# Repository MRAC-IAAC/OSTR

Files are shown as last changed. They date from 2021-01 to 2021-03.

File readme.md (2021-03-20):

SHEDIO [ _Σχέδιο_ ] --
_noun_
- from Greek origin meaning _'plan', 'drawing', 'scheme'_

-------------------------------

## **IAAC - MRAC 01**

## **DRAWING BOT - HARDWARE II SEMINAR**

**- A minibot that draws contours of images on flat surfaces -**

-------------------------------

### **The Drawing Bot**
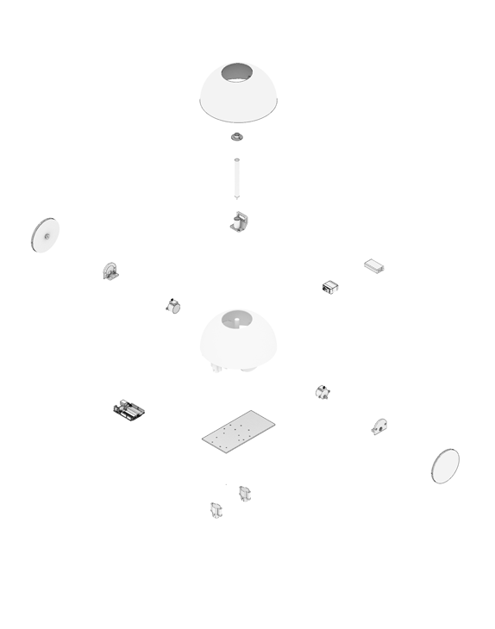
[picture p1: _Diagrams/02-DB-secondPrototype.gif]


-------------------------------

## **GETTING STARTED**

**_Note_**  
For this DIY project, a separate setup of the piCamera (in a box) is in charge of taking the photo that is to be traced by the mini bot.  

Let's do it!

-------------------------------

## **00. HARDWARE**

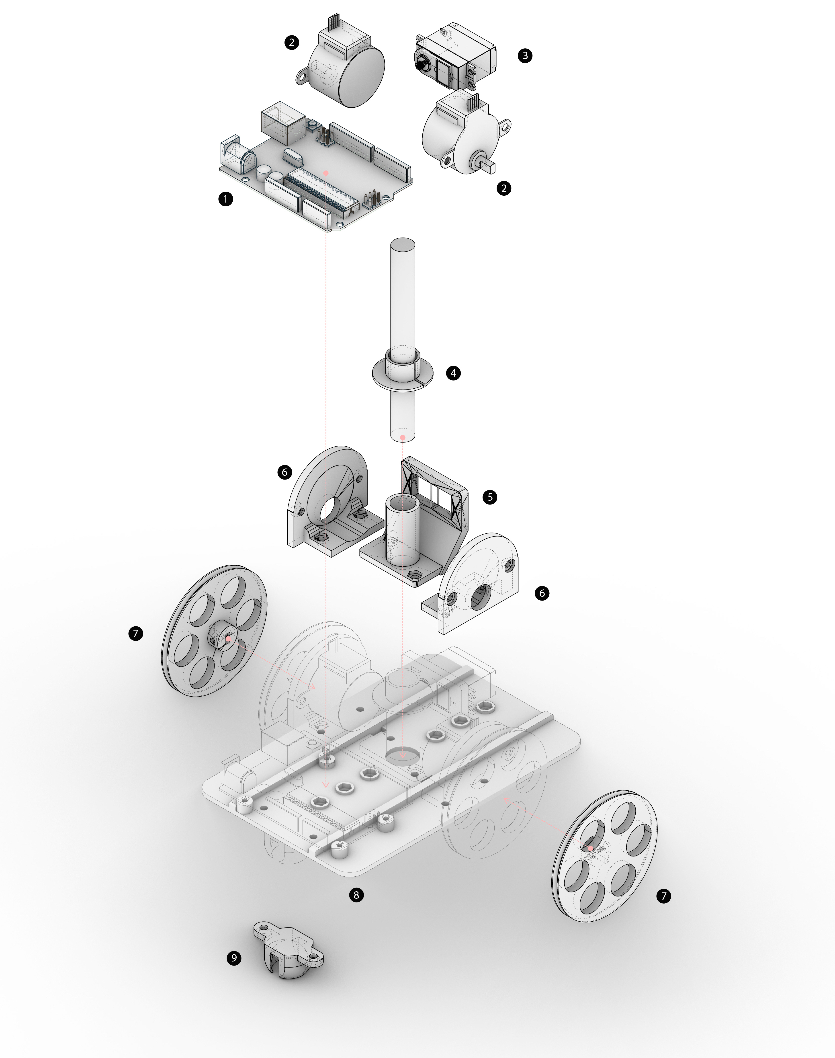
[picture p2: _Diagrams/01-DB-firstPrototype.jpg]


**First Iteration Parts:**  
(1) Arduino Uno  
(2) 28byj-48 Stepper Motor (x2)  
(3) Mini Servo Motor  
(4) Pen Holder  
(5) Servo Motor Holder (controlling the pen’s movement)  
(6) 3D Printed Wheels (x2)  
(7) 3D Printed Board  
(8) Base Plate  
(9) Ball Bearing Holder  

**_Note_**  
An updated model with the latest parts can be found in the _Hardware folder [here](https://github.com/MRAC-IAAC/SHEDIO/tree/master/_Hardware/3D%20Models).

-------------------------------

## **01. ARDUINO**

### **CALIBRATING THE ROBOT & UNDERSTANDING THE SCRIPT**

First things first, we need to translate string commands into wheel movements (controlled by the motors) to be able to establish a clear language with the mini bot. For that, we also need to calibrate it properly.

Follow the tutorial through this [link](https://www.instructables.com/Arduino-Drawing-Robot/).

All necessary arduino codes can be found [here](https://github.com/MRAC-IAAC/SHEDIO/tree/master/_Scripts/Arduino_codes) with comments. 

-------------------------------

## **02. RASPBERRY PI**
**Operating System:** Raspbian GNU/ Linux 10 (buster)

For beginners in Raspberry Pi, [this link](https://www.raspberrypi.org/software/) will be useful to download the imager in order to flash a microSD card with the Raspberry Pi OS. 
The [documentation](https://www.raspberrypi.org/documentation/) tab in the official raspberry pi website is very useful to set up the pi. In the diagrams folder, there is an image of the pinout diagram for the Raspberry Pi 4. 

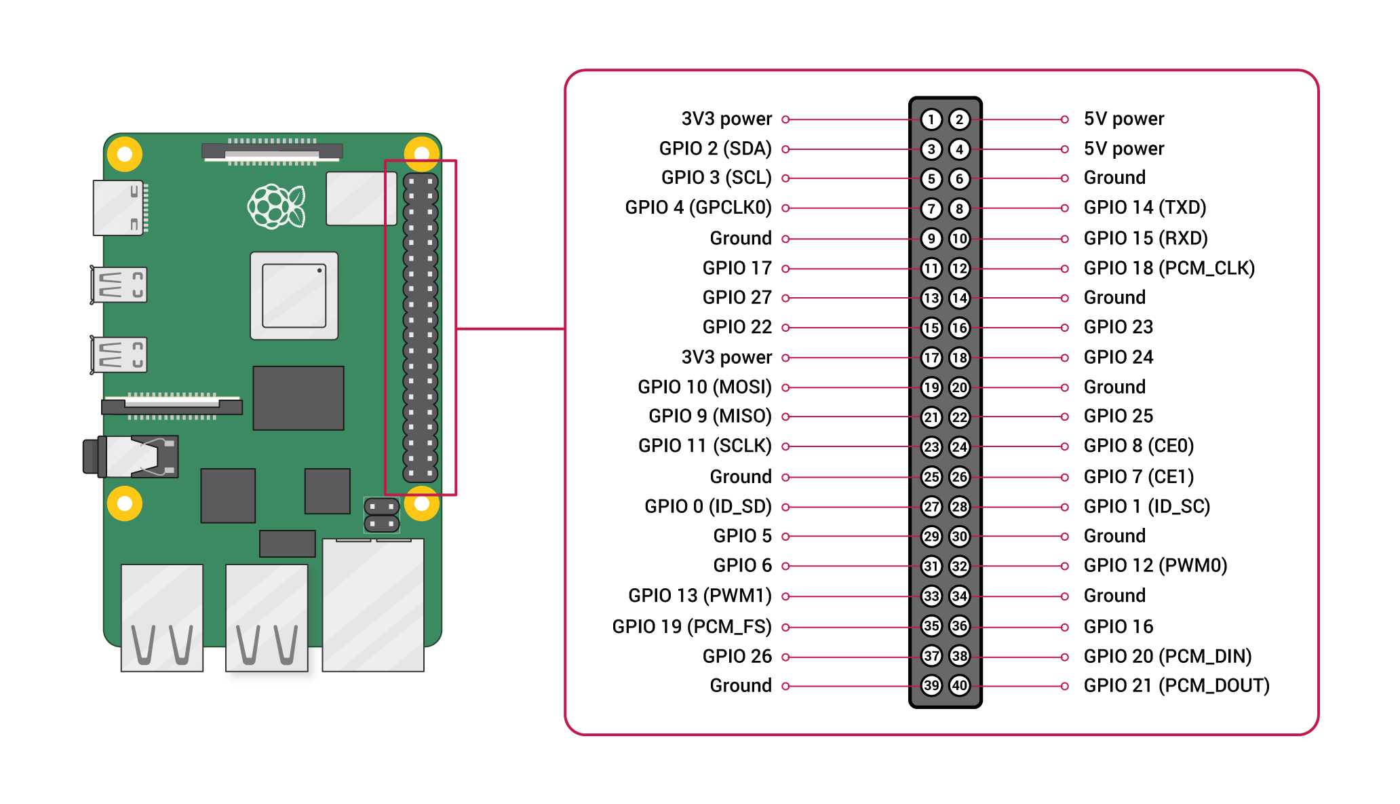
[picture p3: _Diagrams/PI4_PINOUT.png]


The scripts folder should contain a test script to run the pi camera with a touch sensor/ button and another test script for the LED's. 

Some links we used on top of the general set up are as follows:

- PI CAMERA SETUP: https://projects.raspberrypi.org/en/projects/getting-started-with-picamera/2
- BUTTON EXAMPLE: https://raspberrypihq.com/use-a-push-button-with-raspberry-pi-gpio/

### **BLUETOOTH SETUP**
Seting up bluetooth to connect to the HC-06 on the arduino:
This takes a couple of steps to get it to work properly. First, you will have to make sure your Pi is set up with bluetooth properly.

Open a terminal and type
```
bluetoothctl
agent on
default-agent
scan on
```
This will show you a list of available bluetooth networks nearby. You will have to locate the name of your bluetooth and copy the IP address. 

Open a new terminal and do the following:
```
sudo nano /etc/bluetooth/rfcomm.conf
```
add the following and replace the device ip address with yours
```
rfcomm0{
    bind yes;
    device AA:BB:CC:DD:EE:FF
    channel 1;
    comment "connection to bluetooth serial module";
}
```
This will create the necessary file in order for the Raspberry Pi to recognize and connect with the HC-06 Bluetooth Module. You will need to reboot your pi, and once restarted, type the following:

```
bluetoothctl
agent on
default-agent
scan on
```
And in a new terminal:
```
sudo rfcomm connect hci0 AA:BB:CC:DD:EE:FF
```
Now you should be connected to your bluetooth device. In order to connect to your bluetooth module using python, you will have to download the **pyserial** package and your serial port should be defined as (in your python script):
```
 /dev/rfcomm0 
 ```
The name is rfcomm0 because that is the name we wrote in the **rfcomm.conf** file in order for the Raspberry Pi to recognize the bluetooth module. If you need to check, you can type the following into a terminal, which will give you a list of devices connected to your Raspberry Pi via serial port. 
```
lsusb
```

In order to take a picture and translate that into directions, run the **final_script.py** file and then to operate the drawing bot, run the **send_all_the_instructions_to_arduino.py** file (that is where you might have to change the serial port)

**NOTE: The scripts are explained below, and there are notations in each file**

### **OTHER USEFUL LINKS**

Some other links regarding connecting to the Raspberry Pi remotely

To set up a usb connection between the pi and your laptop:
- https://www.hardill.me.uk/wordpress/2019/11/02/pi4-usb-c-gadget/

To set up putty:
- https://www.factoryforward.com/pi-zero-w-headless-setup-windows10-rndis-driver-issue-resolved/

To set up VNC Viewer:
- https://www.raspberrypi.org/documentation/remote-access/vnc/

-------------------------------

## **03. PYTHON**

**_Note_**  
During this project, the following OS and code editors (not necessary) were used:

**Operating Systems:** macOS, Microsoft Windows and Linux  
**Editor 1:** Visual Studio Code, found [here](https://code.visualstudio.com/)  
**Editor 2:** Pycharm, found [here](https://www.jetbrains.com/pycharm/)

For beginners in Python, the [official website](https://www.python.org/about/gettingstarted/) offers getting started tips.  
 **Socratica's** fun youtube [tutorial](https://www.youtube.com/playlist?list=PLi01XoE8jYohWFPpC17Z-wWhPOSuh8Er-) also provides a step by step guide into the basics of Python.   
 This code uses Python 3.9.

 First start by creating a custom environment for this project, to eventually install necessary libraries. Follow the tutorial on how to do so [here](https://docs.python.org/3/library/venv.html).

For this code, available in the _Scripts folder of the repository [here](https://github.com/MRAC-IAAC/SHEDIO/blob/master/_Scripts/Python_codes/final_script.py), you will need to install the following libraries:  
- [OpenCV](https://docs.opencv.org/master/df/d65/tutorial_table_of_content_introduction.html) library  
- [Numpy](https://numpy.org/install/) library

Understanding the basic of how to find and draw contours using the **OpenCV** library can be found [here](https://docs.opencv.org/master/d4/d73/tutorial_py_contours_begin.html). A simple code can be found [here](https://gitlab.com/fablabbcn-projects/learning/code-club/-/blob/2020/04_computer_vision/02_findcontours.py).

A visual introduction to **Numpy** can be found [here](http://jalammar.github.io/visual-numpy/) for a better understanding of the library and how it works.

A basic explanation of the logic of the code and how it works can be found in this [blogpost](http://www.iaacblog.com/programs/drawing-bot-hardware-ii-seminar/) under "Python Script".

**_Note_**  
The current Python script does not work properly yet, meaning that the robot does not draw the contours properly. We were not able to fully develop the code in the time frame we had so any notes or advice are welcome. We will continue to work on it and update this repo during our free time. 

-------------------------------

## **04. FABRICATION**

The necessary parts for this bot were 3D printed. Find the catalogue of parts [here](https://github.com/MRAC-IAAC/SHEDIO/tree/master/_3D%20Print%20Files).  

**You will need:** 
- x1 base 
- x2 wheels
- x2 stepper motor holders
- x1 pen holder 
- x1 servo motor holder 
- x2 ball bearing holder
- x2 ball bearing extentions
- x1 cap 

**You will also need:** 
- x6 screws [M3 x 10] for the base
- x4 screws [M3 x 30] for the extensions
- x10 M3 nuts

The final model should look like this:
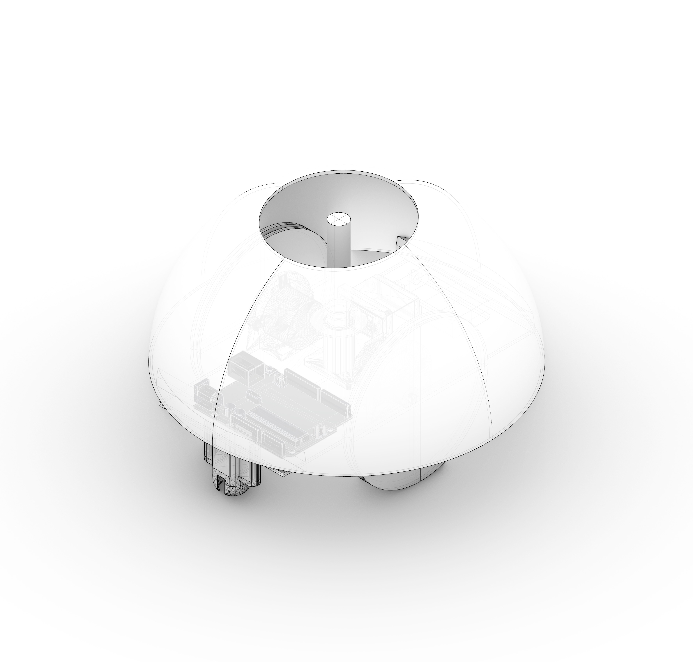
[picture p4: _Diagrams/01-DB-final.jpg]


**piCamera Box:**  
The piCamera Box can be fabricated through [CNC](https://github.com/MRAC-IAAC/SHEDIO/tree/master/_Fabrication%20Files/CNC) or [Lasercut](https://github.com/MRAC-IAAC/SHEDIO/tree/master/_Fabrication%20Files/Lasercut). We chose to CNC and eventuallty sand the parts to create the frost effect. 

**_Note_**  
You might need to adjust the Lasercut dimensions should you choose a different material (we used 6 mm acrylic).

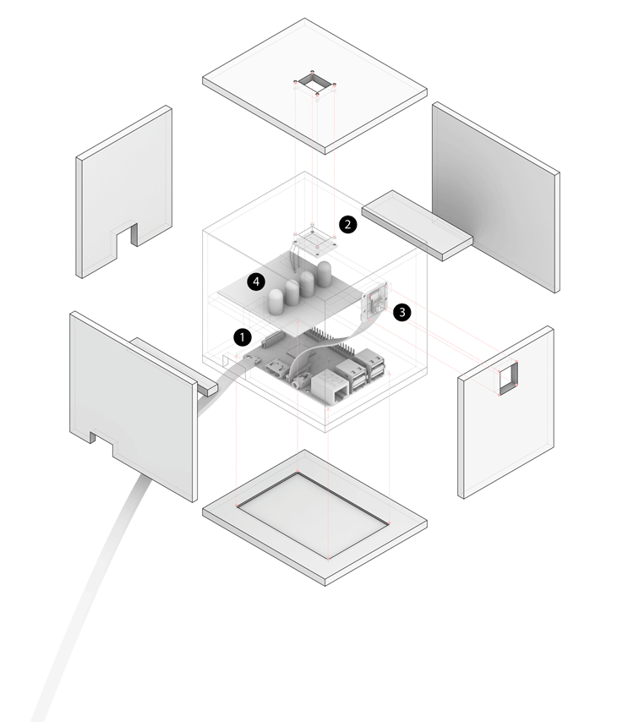
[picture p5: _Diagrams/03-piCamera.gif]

(1) Raspberry Pi 4B  
(2) Touch Sensor  
(3) PiCamera  
(4) Board of LEDs  

-------------------------------

## **CREDITS**

-------------------------------

**DRAWING BOT - HARDWARE II SEMINAR** is a project of **IAAC, Institute for Advanced Architecture of Catalonia**, developed in the **Master in Robotics and Advanced Construction** in 2020/2021 by:

**Students:** Aslinur Taskin, Helena Homsi and Juan Eduardo Ojeda  
**Faculty:** Oscar Gonzalez  
**Faculty Assistant:** Antoine Jaunard

-------------------------------

**Reach us at:**  

_Aslinur Taskin:_ aslinur.taskin@students.iaac.net  
_Helena Homsi:_ helena.homsi@students.iaac.net  
_Juan Eduardo Ojeda:_ juan.eduardo.ojeda@students.iaac.net

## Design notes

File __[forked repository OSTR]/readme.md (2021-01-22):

Open Source Turtle Robot (OSTR)
-------------------------------

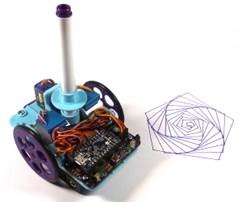
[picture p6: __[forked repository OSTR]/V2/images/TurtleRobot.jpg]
ChickTech Robot
 
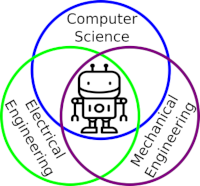
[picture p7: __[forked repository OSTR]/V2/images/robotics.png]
Robotics Engineering Fields
 

I designed this project for a 10-hour workshop for [ChickTech.org](http://www.chicktech.org) whose goal is to introduce teenage women to STEM topics. The goals for this project were:

- Easy to build.
- Easy to program.
- Did something interesting.
- Low-cost so participants could take it home and continue to learn.

Robotics is the exciting intersection of a number of engineering fields including mechanical engineering, electrical engineering, and computer science. This project was designed to make learning about these fields accessible and exciting.

Turtle robots are controled by simple instructions like "forward(distance)" and "left(degrees)", and their visual tracks are instructive as well as entertaining. They also demonstrate how systems with simple rules can have complex behaviors, something we see in nature all the time.

New to Version 2 is the shift from the Adafruit [Trinket Pro](https://www.adafruit.com/product/2010) to their [ItsyBitsy 32U4 3V](https://www.adafruit.com/product/3675) which enables USB communication for easier troubleshooting, or the [ItsyBitsy M0 Express](https://www.adafruit.com/product/3727) which allows programing in Python!

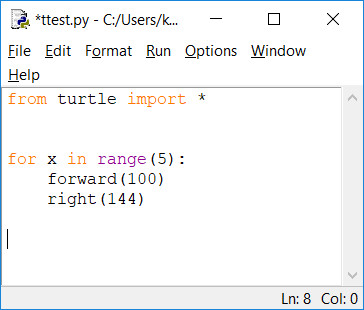
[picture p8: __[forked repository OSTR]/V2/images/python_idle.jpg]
Turtle Python commands in Idle
 
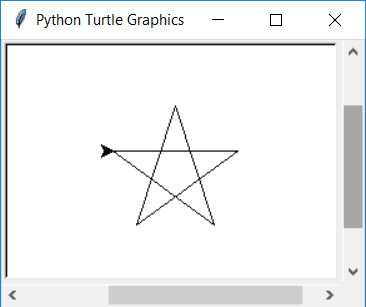
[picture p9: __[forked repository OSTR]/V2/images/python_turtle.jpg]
Turtle Graphics
 

Python is a popular and easy to learn programming language that already has Turle Graphics built in.  Since the robots instructions are the same, programs and paterns can be evaluated on the computer and then run on the robot. 
```python
from turtle import *

for x in range(5):
    forward(100)
    right(144)
```

Here is a great Hour of Code tutorial to get you introduced to Python Turtle: [https://groklearning.com/hoc/activity/snowflake/](https://groklearning.com/hoc/activity/snowflake/).  The only thing pysical Turtle Robot can't do is change colors automatically, but you can alway swap the pens around manually.

### Video of Turtle Robot (V1) in action:

IMAGE ALT TEXT HERE (https://www.youtube.com/watch?v=j0FpB0iv0v0)

This robot has been refined through a number workshops, but still has room for improvement.  Please share your ideas and modifications so it can continue to improve.

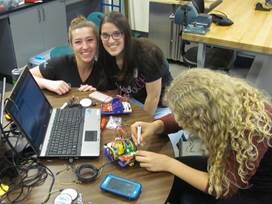
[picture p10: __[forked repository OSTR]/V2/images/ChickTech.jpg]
ChickTech Workshop
 

Bill Of Materials
-----------------
In bulk quantities, the cost per robot is about $40.  The Bill of Materials is available [here](/V2/BOM.md).
Having told you the at-cost and provided you my BOM, I'd still offer to [sell you a kit](https://www.tindie.com/products/MakersBox/open-source-turtle-robot-ostr/) if you'd like to pay for the convenience of a single-source or you don't have access to a 3D printer.  This also allows me continue development for future workshops.

Tindie

Design Files
------------
The electronics were designed using Open Source [KiCad](http://kicad-pcb.org/). Design files are located in the [design_files](V2/design_files/) folder.  You can oogle the [schematic](V2/docs/Schematic.pdf).

The 3D Design files were created with a combination of [FreeCad](https://www.freecadweb.org/), [OpenSCAD](https://www.openscad.org/) (both Open Source), and online [TinkerCad](https://www.tinkercad.com/).  Design files and STLs are located in the [3D](V2/3D/) folder.

Firmware
--------
This project is programed using Open Source [Arduino](https://www.arduino.cc/) or Adafruit's [Circuit Python](https://learn.adafruit.com/welcome-to-circuitpython/what-is-circuitpython) depending on the microcontroller used. The firmware is located in the [firmware](V2/firmware/) folder.  Instructions for setting up the Arduino environment for the ItsyBitsy 32U4 are at [https://learn.adafruit.com/introducting-itsy-bitsy-32u4/](https://learn.adafruit.com/introducting-itsy-bitsy-32u4/).

Assembly Instructions
---------------------
[https://www.instructables.com/id/OSTR/](https://www.instructables.com/id/OSTR/).  
Also, check the [docs](V2/docs/) folder for handouts, etc.  May still have pictures of V1 assembly, but they are nearly identical.

License
-------
[Attribution-ShareAlike 3.0 United States (CC BY-SA 3.0 US)](https://creativecommons.org/licenses/by-sa/3.0/us/)

You are free to:

- Share — copy and redistribute the material in any medium or format
- Adapt — remix, transform, and build upon the material

Under the following terms:

- Attribution — You must give appropriate credit, provide a link to the license, and indicate if changes were made. You may do so in any reasonable manner, but not in any way that suggests the licensor endorses you or your use.
- ShareAlike — If you remix, transform, or build upon the material, you must distribute your contributions under the same license as the original.

Certified Open Source:
----------------------
This project as been certified by the [Open Source Hardward Association](https://certification.oshwa.org/):

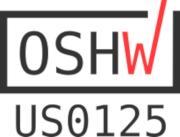
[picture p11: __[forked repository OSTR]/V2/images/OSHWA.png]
OSHWA


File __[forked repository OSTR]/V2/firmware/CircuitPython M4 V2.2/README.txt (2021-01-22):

Turtle Robot (V2.1) https://github.com/aspro648/OSTR/
@TheMakersBox
#TurtleRobot
648.ken@gmail.com

You have an Adafruit ItsyBitsy M4:
    https://learn.adafruit.com/introducing-adafruit-itsybitsy-m4
Running CiruitPython version 4.1.0
    https://learn.adafruit.com/circuitpython-essentials/circuitpython-essentials
Download Mu Editor at https://codewith.mu/en/download

Workshop Links:
  Handouts: https://github.com/aspro648/OSTR/raw/master/V2/docs/Robotics%20Handoouts%202019.pdf
  Mechanical Assembly: https://github.com/aspro648/OSTR/raw/master/V2/docs/Mechanical%20Assembly.pdf
  Name Plate Design: https://github.com/aspro648/OSTR/raw/master/V2/docs/Name%20Plate%203D%20Design.pdf
  
Activites:
  https://www.tinkercad.com/joinclass/6I6RPXA9QDII
  https://groklearning.com/hoc/activity/snowflake/
  https://studio.code.org/s/frozen/stage/1/puzzle/1

#############################
CircuitPython Quick Start:

Changing the code is as easy as editing code.py in your favorite text editor. 

Our recommended editor is Mu, which is great for simple projects, and comes
with a built in REPL serial viewer! It is available for Mac, Windows & Linux
https://learn.adafruit.com/welcome-to-circuitpython/installing-mu-editor

After the file is saved, CircuitPython will automatically reload the latest 
code. Try enabling the single-button keyboard!
         (HINT: look for the "# optional! uncomment below..." text)

Connecting to the serial port will give you access to sensor information, 
better error messages and an interactive CircuitPython (known as the REPL). 
On Windows we recommend Mu, Tera Term or PuTTY. 
On Mac OSX and Linux, use Mu or 'screen' can be used from a terminal.

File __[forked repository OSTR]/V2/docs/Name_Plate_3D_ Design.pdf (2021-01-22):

## Turtle Robot Nameplate

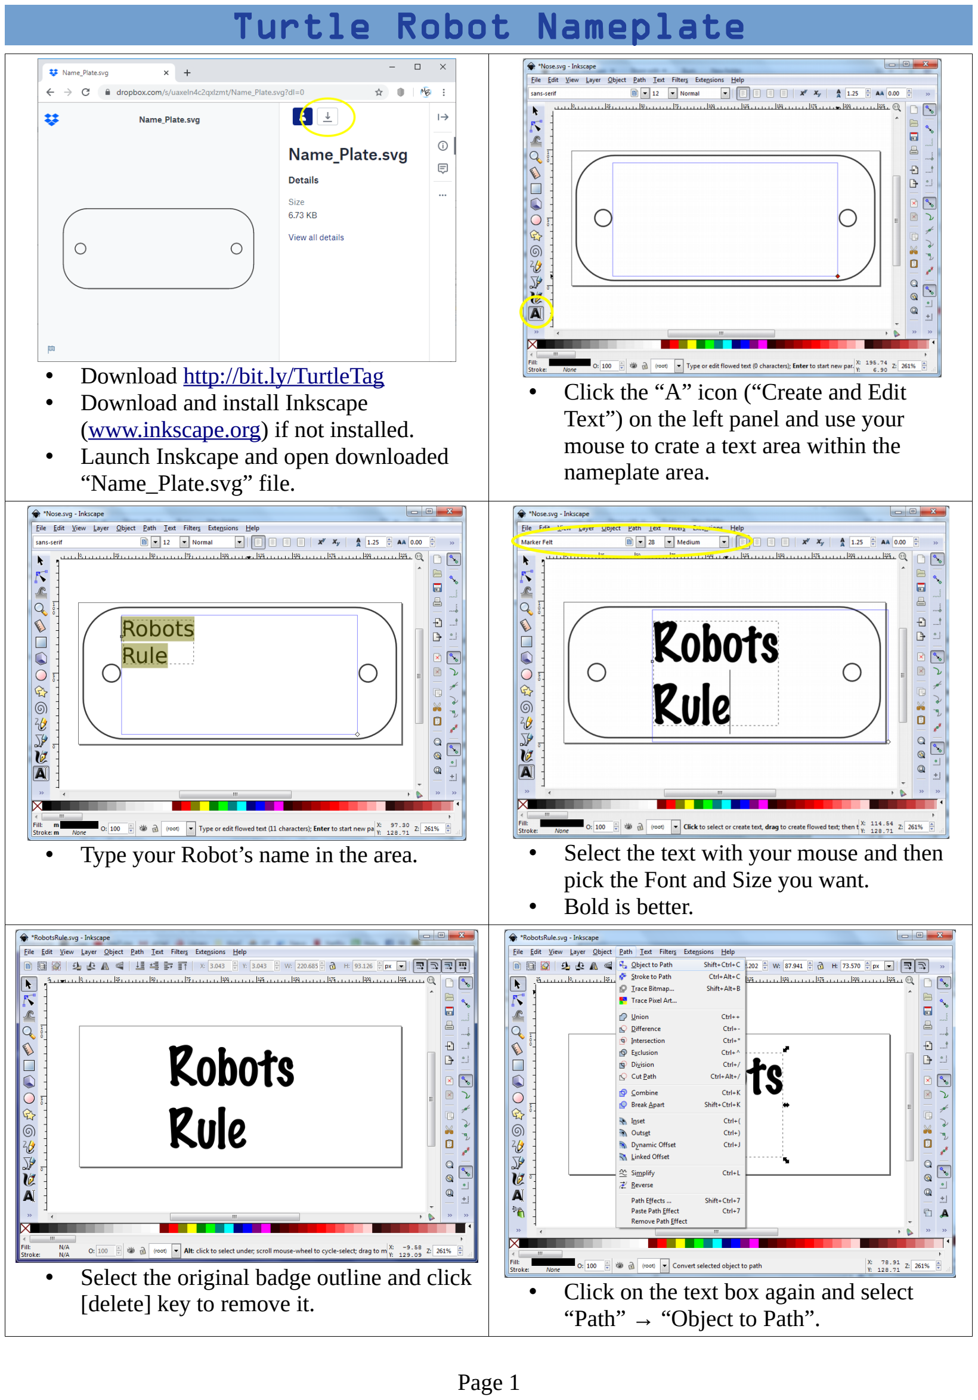
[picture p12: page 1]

- Download http://bit.ly/TurtleTag • Download and install Inkscape (www.inkscape.org) if not installed. • Launch Inskcape and open downloaded “Name_Plate.svg” file. | • Click the “A” icon (“Create and Edit Text”) on the left panel and use your mouse to crate a text area within the nameplate area.
- Type your Robot’s name in the area. | • Select the text with your mouse and then pick the Font and Size you want. • Bold is better.
- Select the original badge outline and click [delete] key to remove it. | • Click on the text box again and select “Path” → “Object to Path”.

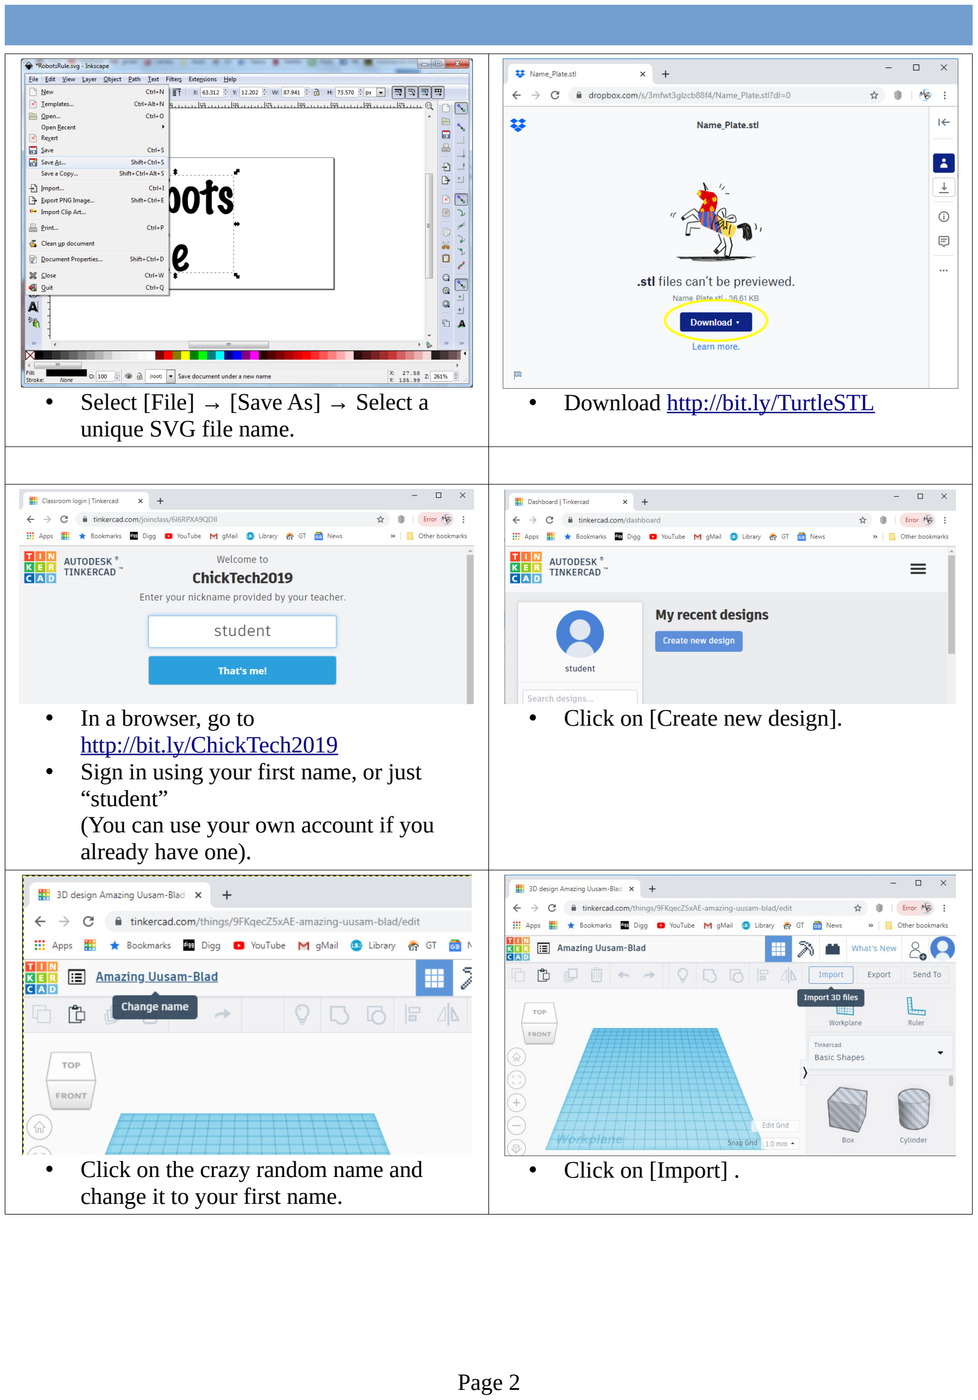
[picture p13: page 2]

- Select [File] → [Save As] → Select a unique SVG file name.
- Download http://bit.ly/TurtleSTL
- In a browser, go to http://bit.ly/ChickTech2019 • Sign in using your first name, or just “student” (You can use your own account if you already have one). | • Click on [Create new design].
- Click on the crazy random name and change it to your first name. | • Click on [Import] .

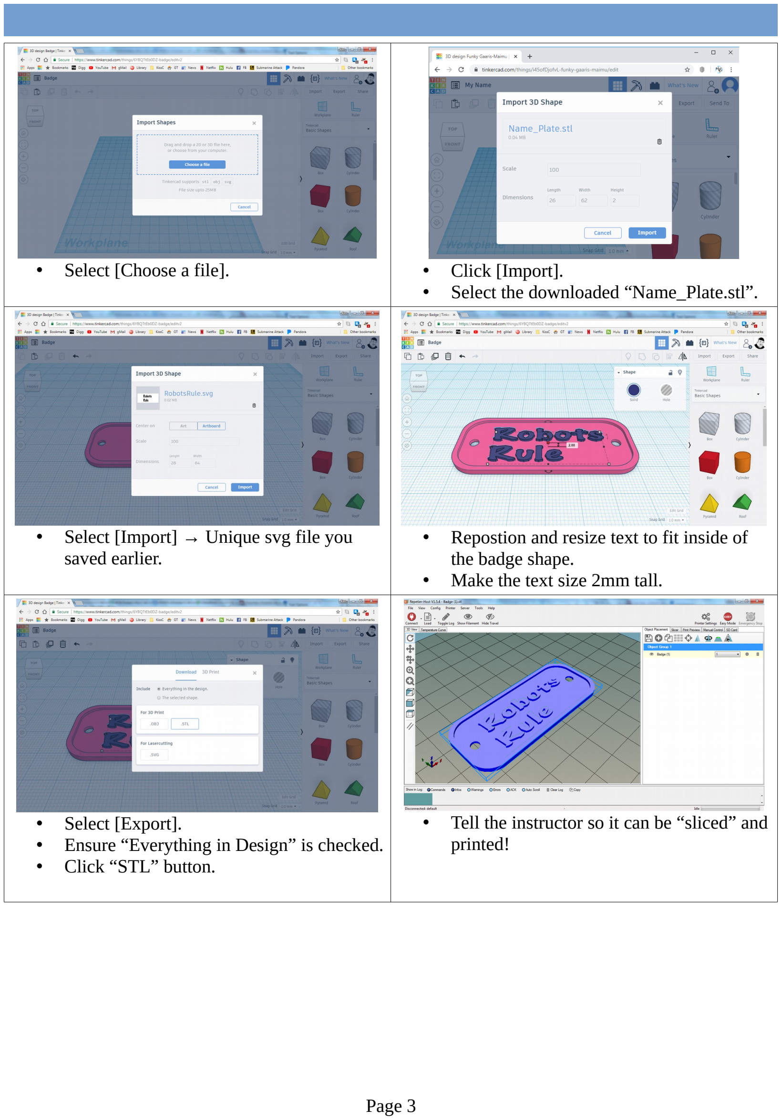
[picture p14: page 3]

- Select [Choose a file]. | • Click [Import]. • Select the downloaded “Name_Plate.stl”.
- Select [Import] → Unique svg file you saved earlier. | • Repostion and resize text to fit inside of the badge shape. • Make the text size 2mm tall.
- Select [Export]. • Ensure “Everything in Design” is checked. • Click “STL” button. | • Tell the instructor so it can be “sliced” and printed!

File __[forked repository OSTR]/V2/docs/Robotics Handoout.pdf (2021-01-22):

# Open Source Turtle Robot

What is a robot? Robots are

machines that are programmed

to react to and manipulate their

environments.

Which of the following would

you consider to be a robot?

❏ | Mars Rover
❏ | 3D Printer
❏ | Autonomous Car
❏ | Artificial Arm
- Robotics is the exciting intersection of a number of engineering fields including mechanical engineering, electrical engineering, and computer science. This project was designed to make learning about these fields accessible and exciting.
- Open Source means every aspect of its design from its 3D parts, electronics, and software are available for study and modification, making it easy to build, modify, and improve.
- Turtle robots are controlled by simple instructions like
and | , and their visual tracks are instructive as well as entertaining.
They also demonstrate how systems with simple rules can have complex behaviors, something we see in nature all the time.

## Going Further:

- Build a Turtle Robot of your own from Instructables: http://bit.ly/OSTurtle
- Play with Turtle graphics online at :
- https://blockly-games.appspot.com/ (block programming)
- http://bit.ly/ttturtle (JavaScript)
- https://groklearning.com/hoc/activity/snowflake/ (Python)
- Do an “Hour of Code” activity at https://hourofcode.com/us/learn
- Check for Maker Spaces or programs in your community or at the library.
- ChickTech Workshops: https://chicktech.org/
Ken Olsen | @TheMakersBox | 648.ken@gmail.com

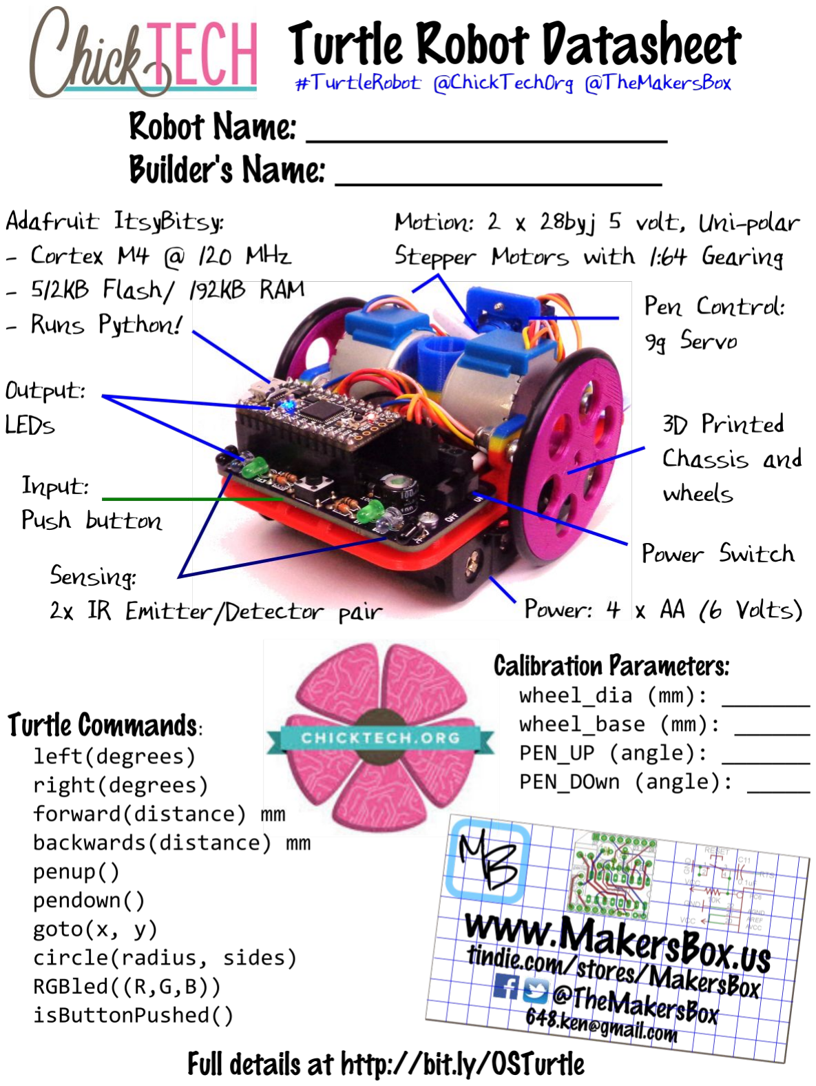
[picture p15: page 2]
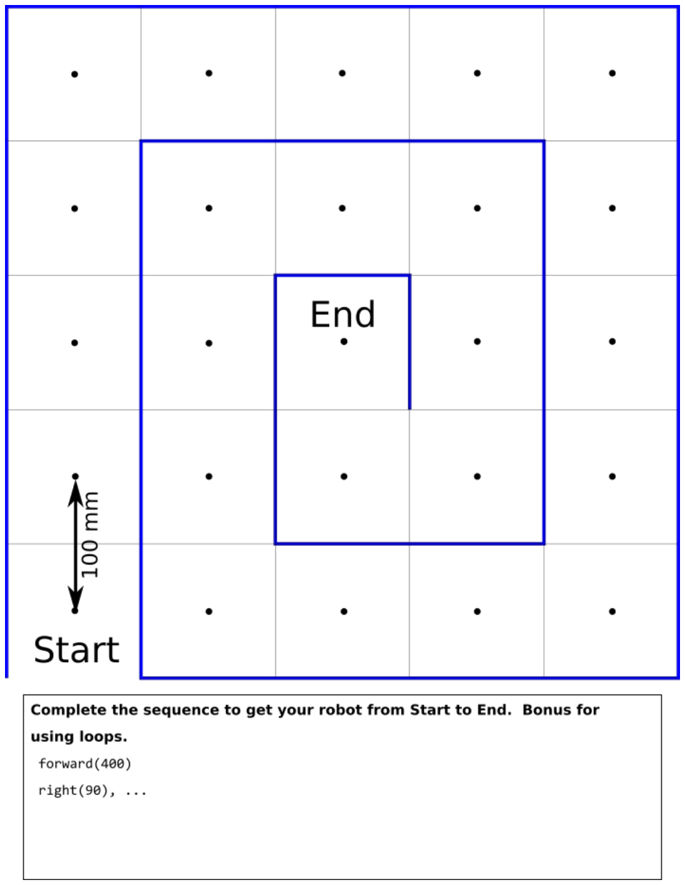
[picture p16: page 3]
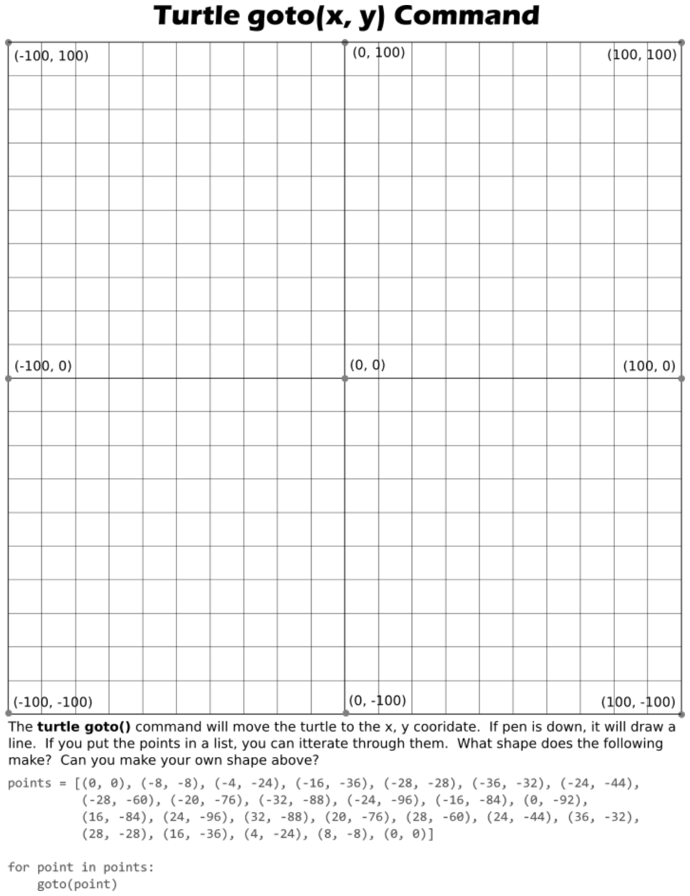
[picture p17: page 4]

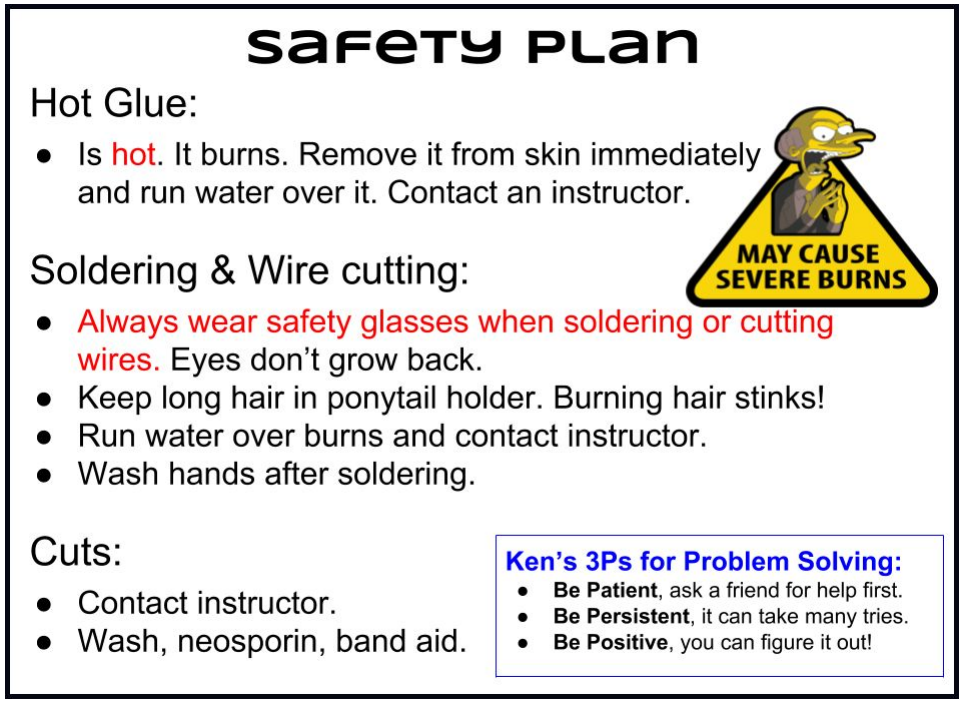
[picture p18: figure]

# Challenge Activities:

- From the snowflake tutorial, create your own custom snowflake and put the code in my_snowflake.py template
- In snowflake examples, use the function random.randint(low, high) to generate random number of arms, angles, and/or lengths.
- In turtle_obstacles.py, the turtle only stops when sensing a wall. Write code to have turtle navigate away from obstacles it senses.
- Try the different songs in rttt_example.py to find your favorite.
- Open music_example.py to see how tones are played. Can you adapt your favorite tune in code?
- What does turtle_goto_example.py draw? Use the handout to create your own object.
- There is a isButtonPushed() function that returns True if pushed, False if not. What could you use that for? Hint: look in turtle_eye_check.py!
- Bonus level: Since turtle can see and emit IR, with a friend could you create a predator / prey pair, with one seeking IR, and the other fleeing IR?

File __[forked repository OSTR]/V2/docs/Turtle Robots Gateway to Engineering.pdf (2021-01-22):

# Turtle Robots:

# Gateway to Engineering

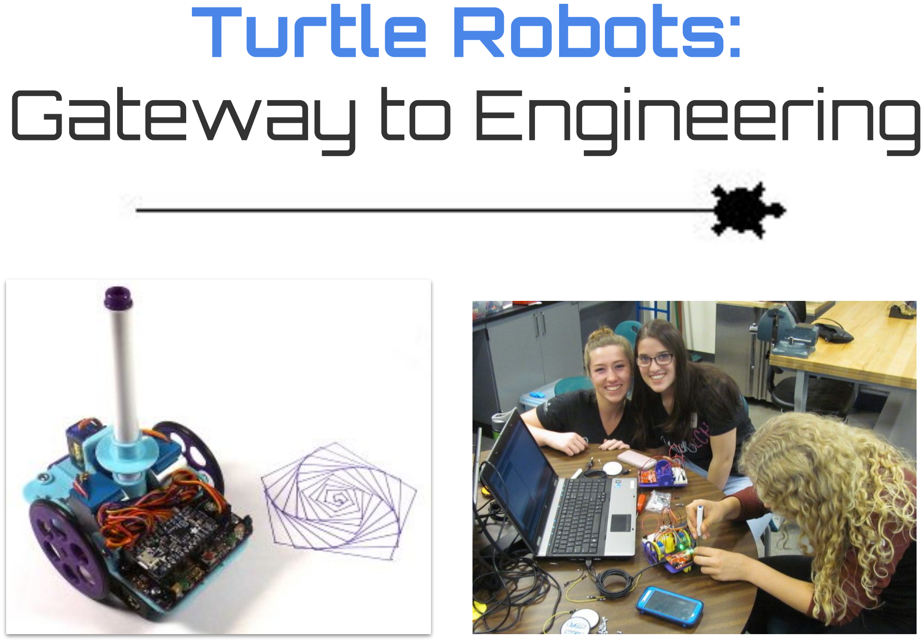
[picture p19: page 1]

# Who Am I?

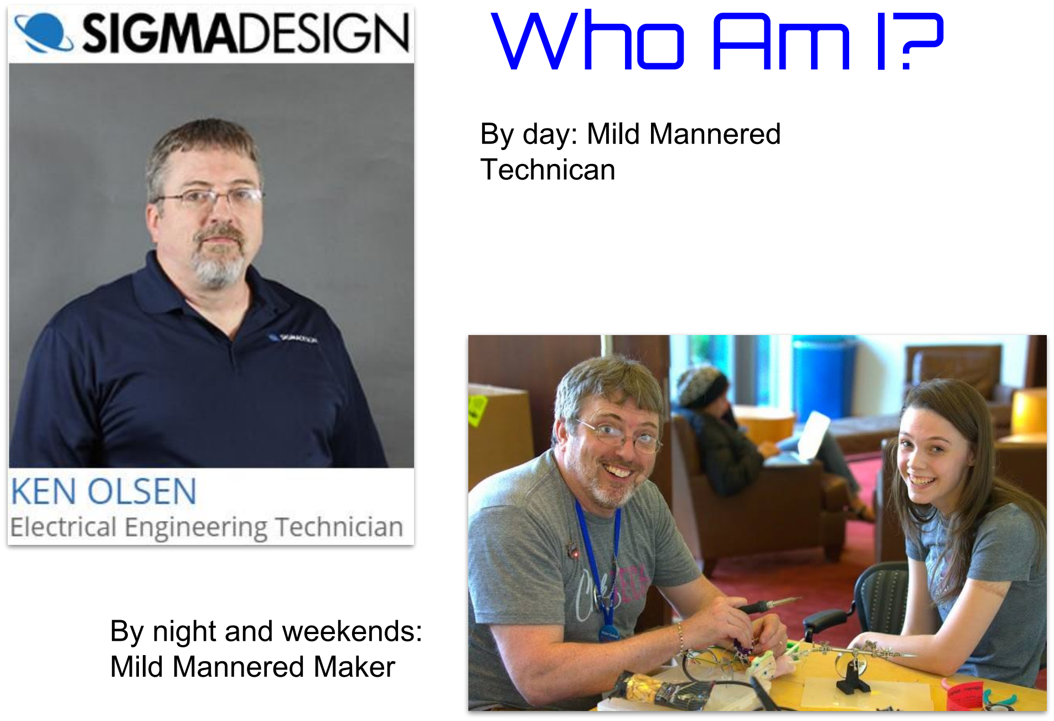
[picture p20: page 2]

By day: Mild Mannered
Technican

By night and weekends:
Mild Mannered Maker

### What is a Turtle Robot?

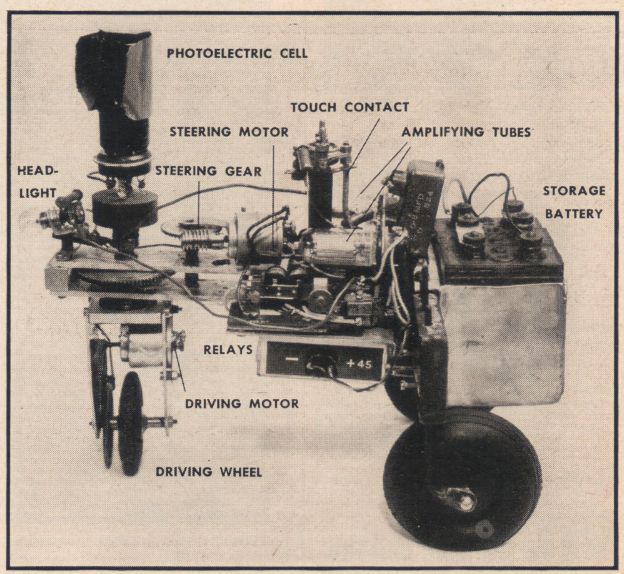
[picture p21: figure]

Grey Walter Tortise circa 1948

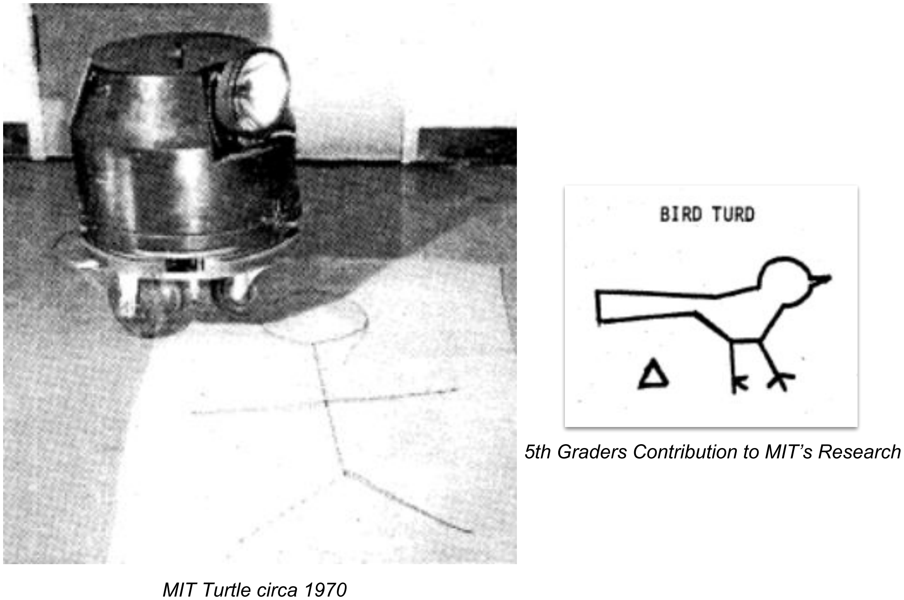
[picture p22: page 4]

MIT Turtle circa 1970

5th Graders Contribution to MIT’s Research

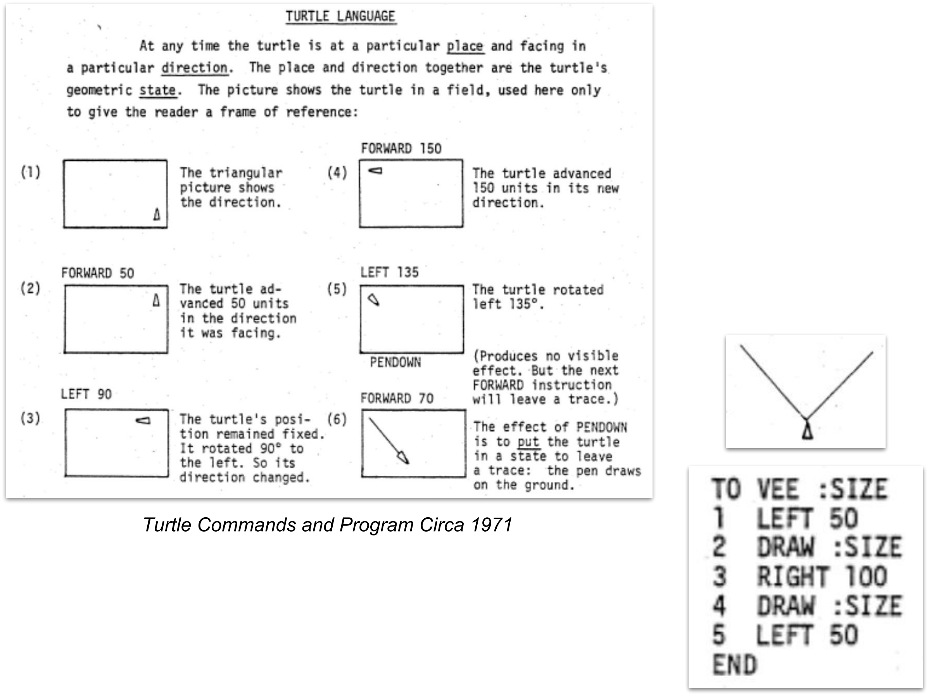
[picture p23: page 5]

Turtle Commands and Program Circa 1971

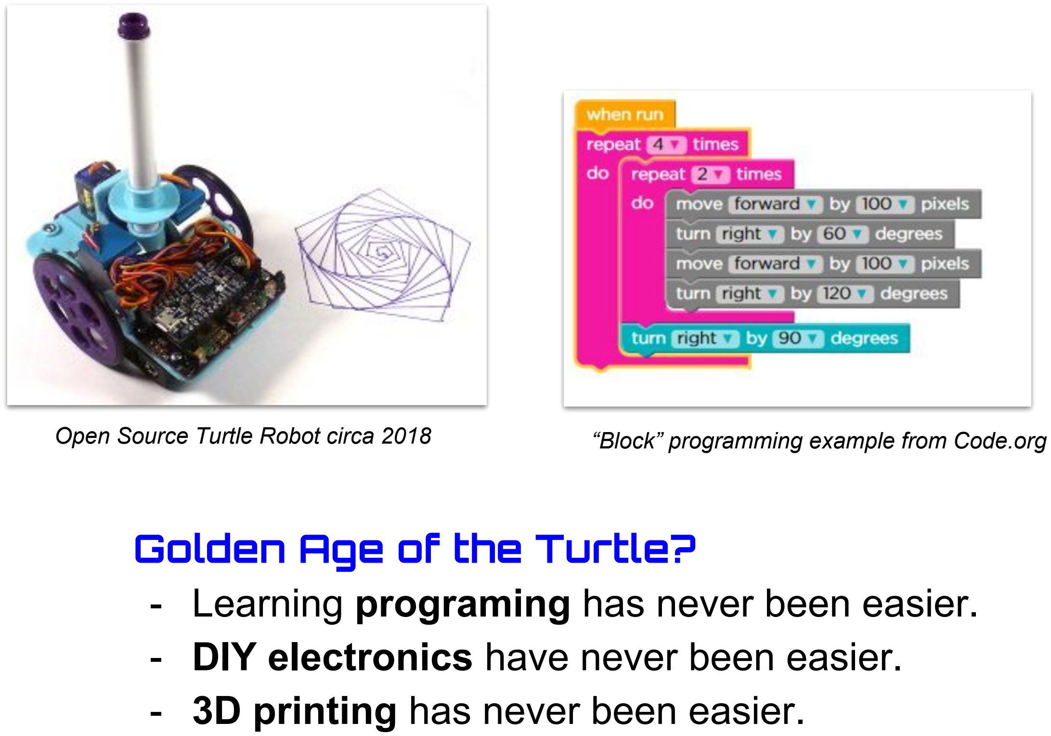
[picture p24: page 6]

Open Source Turtle Robot circa 2018 | “Block” programming example from Code.org

### Golden Age of the Turtle?

- Learning programing has never been easier.
- DIY electronics have never been easier.
- 3D printing has never been easier.

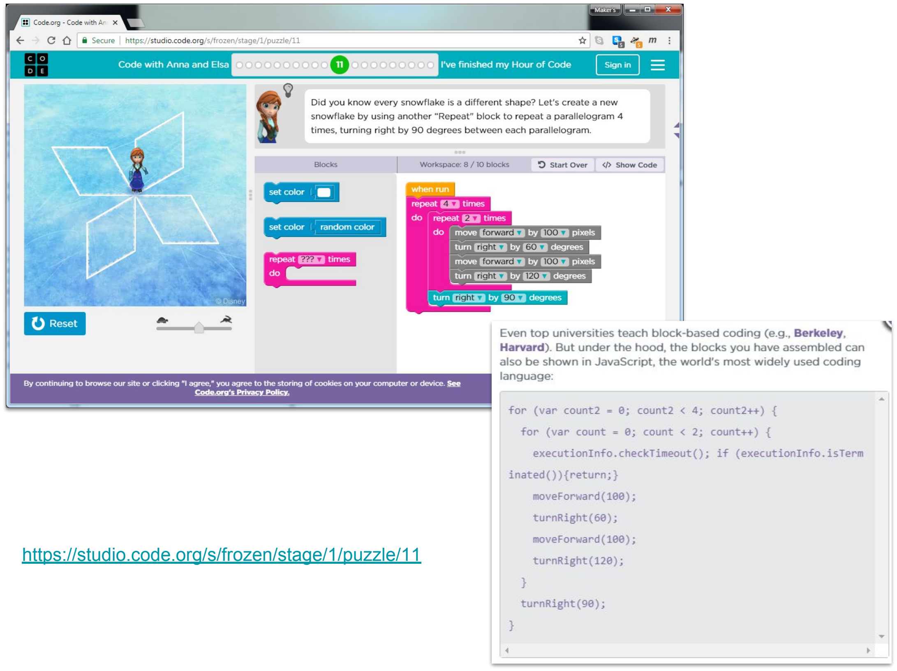
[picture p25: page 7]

https://studio.code.org/s/frozen/stage/1/puzzle/11

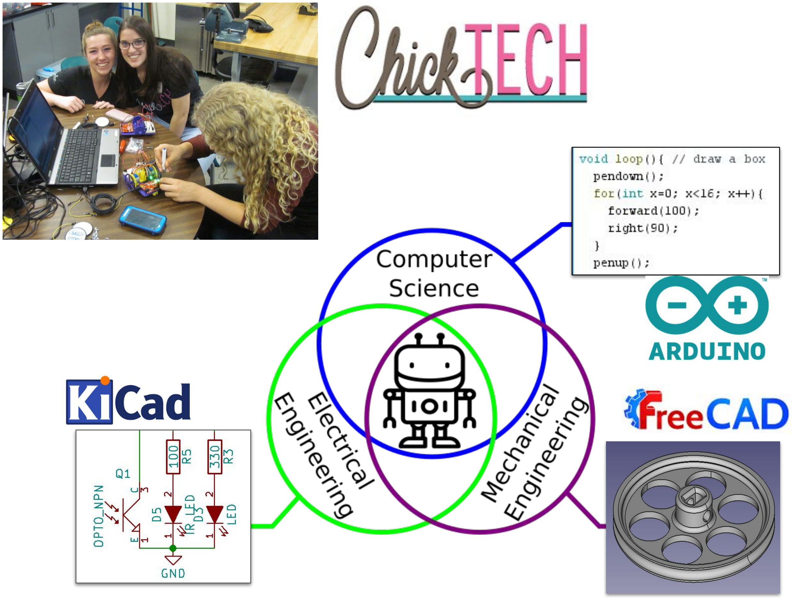
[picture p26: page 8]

### What now?:

- Play with Turtle graphics online at :
- https://blockly-games.appspot.com/ (block programming)
- http://bit.ly/ttturtle (JavaScript)
- Do an “Hour of Code” activity at https://hourofcode.com/us/learn
- Do a 3D design tutorial at https://www.tinkercad.com
- Find out if your library or local makers space will print your design
- Build and program a Turtle Robot of your own: http://bit.ly/OSTurtle
- Make it better and share your results!

### 648.ken@gmail.com

### @TheMakersBox #TurtleRobot

### Slide Deck @ http://bit.ly/OMSIturtle

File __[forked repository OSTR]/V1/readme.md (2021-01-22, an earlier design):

Open Source Turtle Robot (OSTR)
============

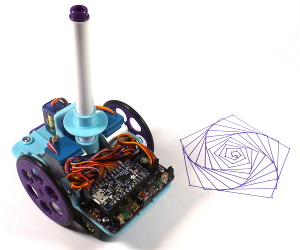
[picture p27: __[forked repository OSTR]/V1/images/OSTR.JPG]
Open Source Turtle Robot
 

Robotics is the exciting intersection of a number of engineering fields including mechanical engineering, electrical engineering, and computer science.  This project was designed as the basis for a two-day workshop for high school age students to introduce them to engineering principles and giving them a jumping off point for exploring their interests further.  There is something for everyone here, even if it is just for the art it creates. The design goals were:

- Easy to build.
- Easy to program.
- Did something interesting.
- Low-cost so participants could take it home and continue to learn.

With those goals in mind, here were a couple of the design choices:

- Arduino compatible for ease of programming.
- 4xAA battery power for cost and availability.
- Stepper motors for accurate motion.
- 3D Printed for ease of customization.
- Pen plotting with Turtle graphics for interesting output.
- Open Source so you could make one of your own!

A kit for this project is [available on Tindie](https://www.tindie.com/products/MakersBox/open-source-turtle-robot-ostr/).
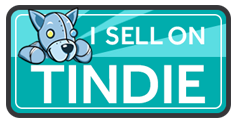
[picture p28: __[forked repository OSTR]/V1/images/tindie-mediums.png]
Tindie Dog (https://www.tindie.com/products/MakersBox/open-source-turtle-robot-ostr/)


Bill Of Materials
-----------------

- [Bill of Materials](BOM.md)

Design Files
------------
The electronics were designed using Open Source [KiCad](http://kicad-pcb.org/). Design files are located in the [electronics](electronics/) folder.  You can oogle the [schematic](electronics/project.pdf).

All 3D STL files located in the [mechanical/STL](mechanical/STL) folder. They were design were designed using:

- [OpenSCAD](http://www.openscad.org/), files located in the [mechanical/OpenSCAD](mechanical/OpenSCAD) folder.
- [FreeCad](https://www.freecadweb.org/), files located in the [mechanical/FreeCad](mechanical/FreeCad) folder.
- [TinkerCad](https://www.tinkercad.com/things/1PzjMSYXagP-oser/editv2) 

Firmware
--------
This project is programed using the Open Source [Arduino](https://www.arduino.cc/). The firmware is located in the [firmware](firmware/) folder.  Instructions for setting up the Arduino enviroment for the Adafruit Trinket Pro are at [https://learn.adafruit.com/introducing-pro-trinket](https://learn.adafruit.com/introducing-pro-trinket).

Assembly Instructions
---------------------
I have published detailed instructions on Instructables at [https://www.instructables.com/id/OSTR/](https://www.instructables.com/id/OSTR/).

License
-------
[Attribution-ShareAlike 3.0 United States (CC BY-SA 3.0 US)](https://creativecommons.org/licenses/by-sa/3.0/us/)

You are free to:

- Share — copy and redistribute the material in any medium or format
- Adapt — remix, transform, and build upon the material

Under the following terms:

- Attribution — You must give appropriate credit, provide a link to the license, and indicate if changes were made. You may do so in any reasonable manner, but not in any way that suggests the licensor endorses you or your use.
- ShareAlike — If you remix, transform, or build upon the material, you must distribute your contributions under the same license as the original.

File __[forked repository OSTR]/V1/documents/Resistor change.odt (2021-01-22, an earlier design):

Resistor substitutions to improve obstacle detection: 100 ohm → 47 ohm (yel-purp-black-gold) 10K ohm → 22K ohm (red-red-orange-gold) | Resistor substitutions to improve obstacle detection: 100 ohm → 47 ohm (yel-purp-black-gold) 10K ohm → 22K ohm (red-red-orange-gold)
Resistor substitutions to improve obstacle detection: 100 ohm → 47 ohm (yel-purp-black-gold) 10K ohm → 22K ohm (red-red-orange-gold) | Resistor substitutions to improve obstacle detection: 100 ohm → 47 ohm (yel-purp-black-gold) 10K ohm → 22K ohm (red-red-orange-gold)
Resistor substitutions to improve obstacle detection: 100 ohm → 47 ohm (yel-purp-black-gold) 10K ohm → 22K ohm (red-red-orange-gold) | Resistor substitutions to improve obstacle detection: 100 ohm → 47 ohm (yel-purp-black-gold) 10K ohm → 22K ohm (red-red-orange-gold)
Resistor substitutions to improve obstacle detection: 100 ohm → 47 ohm (yel-purp-black-gold) 10K ohm → 22K ohm (red-red-orange-gold) | Resistor substitutions to improve obstacle detection: 100 ohm → 47 ohm (yel-purp-black-gold) 10K ohm → 22K ohm (red-red-orange-gold)
Resistor substitutions to improve obstacle detection: 100 ohm → 47 ohm (yel-purp-black-gold) 10K ohm → 22K ohm (red-red-orange-gold) | Resistor substitutions to improve obstacle detection: 100 ohm → 47 ohm (yel-purp-black-gold) 10K ohm → 22K ohm (red-red-orange-gold)

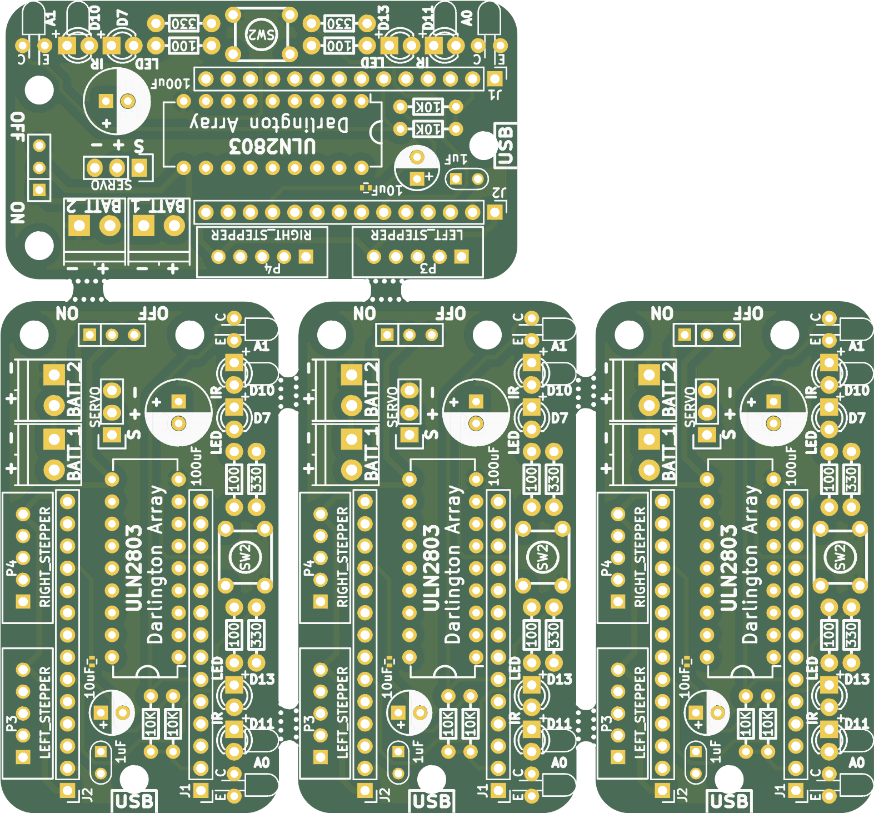
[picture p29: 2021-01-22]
__[forked repository OSTR]/V2/design_files/pannel/pannel_Combined_Top.png

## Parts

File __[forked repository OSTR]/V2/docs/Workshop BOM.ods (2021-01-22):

EE
Quantity | Manufacturer Part Number | Manufacturer | Digi-Key Part Number | Unit Price | Unit Price Q20 | Extended Price
1 | OSH Park | PCB 1.26 x 2.31 |  |  | 2.9106 | 2.9106
2 | B5B-XH-AM(LF)(SN) | JST Sales America Inc. | 455-2239-ND | 0.26 | 0.243 | 0.486
1 | EG1218 | E-Switch | EG1903-ND | 0.61 | 0.582 | 0.582
2 | ED555/2DS | On Shore Technology Inc. | ED1514-ND | 1.06 | 0.563 | 1.126
2 | 2463 | Keystone Electronics | 36-2463-ND | 1.1 | 0.873 | 1.746
1 | SR205E105MAR | AVX Corporation | 478-7667-ND | 0.84 | 0.63 | 0.63
2 | CF18JT100R | Stackpole Electronics Inc. | CF18JT100RCT-ND | 0.1 | 0.036 | 0.072
2 | CF18JT330R | Stackpole Electronics Inc. | CF18JT330RCT-ND | 0.1 | 0.036 | 0.072
2 | CF18JT10K0 | Stackpole Electronics Inc. | CF18JT10K0CT-ND | 0.1 | 0.036 | 0.072
1 | 30044 | SCS | SCP347-ND | 0.12 | 0.12 | 0.12
2 | 151031VS06000 | Wurth Electronics Inc. | 732-5008-ND | 0.16 | 0.16 | 0.32
1 | 1825910-6 | TE Connectivity ALCOSWITCH Switches | 450-1650-ND | 0.11 | 0.11 | 0.11
2 | PPTC141LFBN-RC | Sullins Connector Solutions | S7012-ND | 0.91 | 0.803 | 1.606
1 | IR204 | Everlight Electronics Co Ltd | 1080-1072-ND | 0.39 | 0.22 | 0.22
1 | PT204-6B | Everlight Electronics Co Ltd | 1080-1151-ND | 0.34 | 0.184 | 0.184
1 | B5B-XH-A(LF)(SN) | JST Sales America Inc. | 455-2270-ND | 0.25 | 0.24 | 0.24
1 | ULN2803A | STMicroelectronics | 497-2356-5-ND | 1.19 | 1.07 | 1.07
1 | ED18DT | On Shore Technology Inc. | ED3047-5-ND | 0.23 | 0.181 | 0.181
1 | ECE-A1HKS100 | Panasonic Electronic Components | P997-ND | 0.27 | 0.187 | 0.187
1 | UMA1E101MDD | Nichicon | 493-14503-ND | 0.33 | 0.23 | 0.23
 |  |  |  |  | Total | $12.16
Mech / Elec
2 | Geared 5V Stepper |  |  |  | 2.358 | 4.716
1 | Micro servo |  |  |  | 1.809 | 1.809
1 | USB 2.0 A Male |  |  |  | 1.1 | 1.1 | 240
1 | Adafruit ItsyBitsy M0 Express |  |  |  | 10.76 | 10.76 | 5
1 | Adafruit screw driver | https://www.adafruit.com/product/3284 |  |  | 1.35 | 1.35
1 | Robot sticker | https://www.adafruit.com/product/622 |  |  | 1.5 | 1.5
8 | AA batteries |  |  |  | 0.276875 | 2.215
31 | 3D Printing | grams | $20/kg |  | 0.02 | 0.62
2 | Roseart finetip |  |  |  | 0.16 | 0.32
1 | 6x4x3 box |  |  |  | 0.48 | 0.48
4 | 22 awg ferrule |  |  |  | 0.03495 | 0.1398
 |  |  |  |  | Total | $25.01
Hardware
2 | - 2 ea. 1 7/8" ID x 3/16' O-ring | http://www.mcmaster.com/#9452k47/=yskfyu |  |  | 0.1948 | 0.3896
1 | - 1 ea. Caster 5/8" bearing | http://www.mcmaster.com/#96455k58/=yskbki |  |  | 0.1636 | 0.1636
8 | - 8 ea. M3 x 6mm rounded head screw | https://www.mcmaster.com/#92005a116/=19rb37d |  |  | 0.0276 | 0.2208
4 | - 4 ea. M3 x 6mm flat head screw | http://www.mcmaster.com/#91420a116/=yskru0 |  |  | 0.024 | 0.096
10 | - 10 ea. M3 Nut | http://www.mcmaster.com/#90591a250/=yskc6u |  |  | 0.0212 | 0.212
4 | - 4 ea. #2 x 1/4 thread forming screw | https://www.mcmaster.com/#90380a005/=19o9cmt |  |  | 0.074 | 0.296
2 | zip ties | https://www.amazon.com/gp/product/B077TJ11JR |  |  | 0.01915 | 0.0383
 |  |  |  |  | Total | $1.42
 |  |  |  | Grand Total |  | $38.59

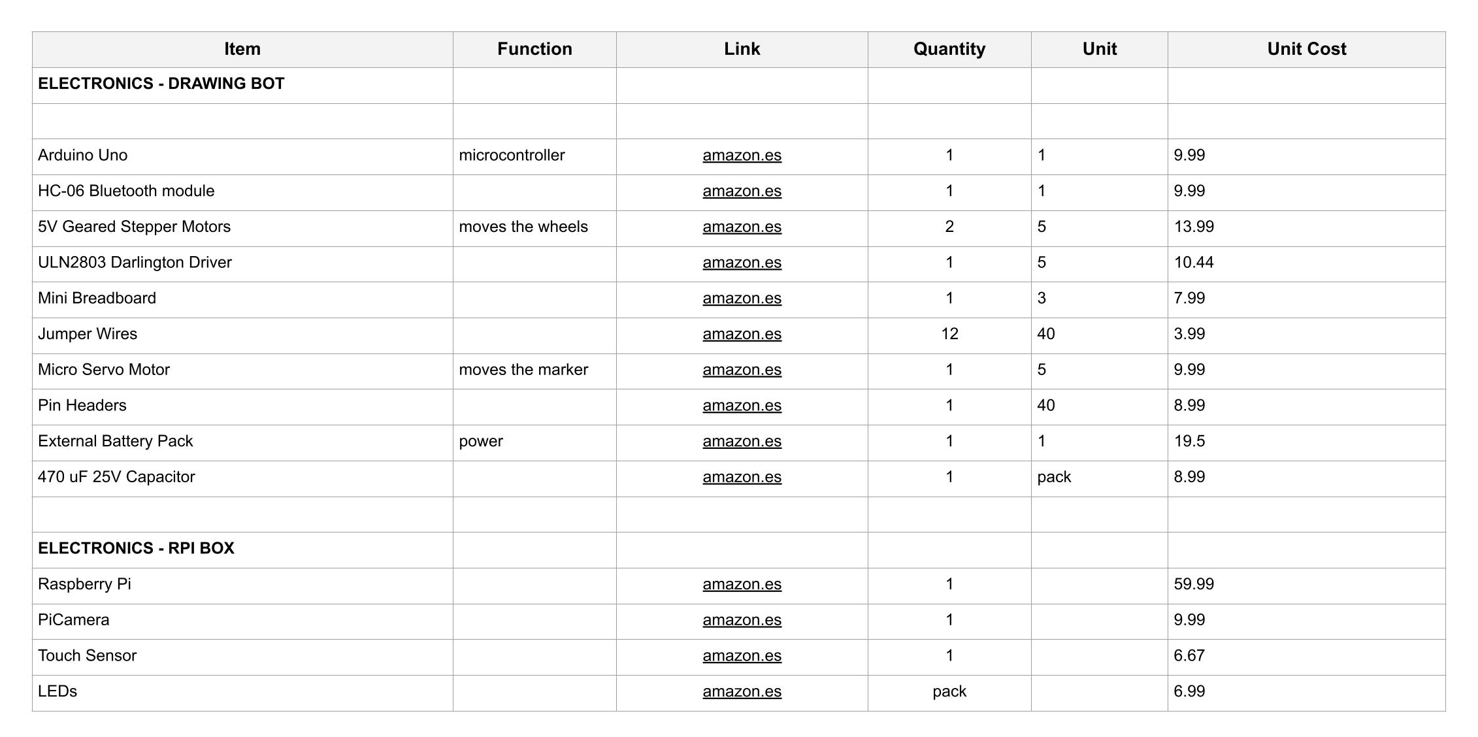
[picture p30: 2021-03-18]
BOM.jpg

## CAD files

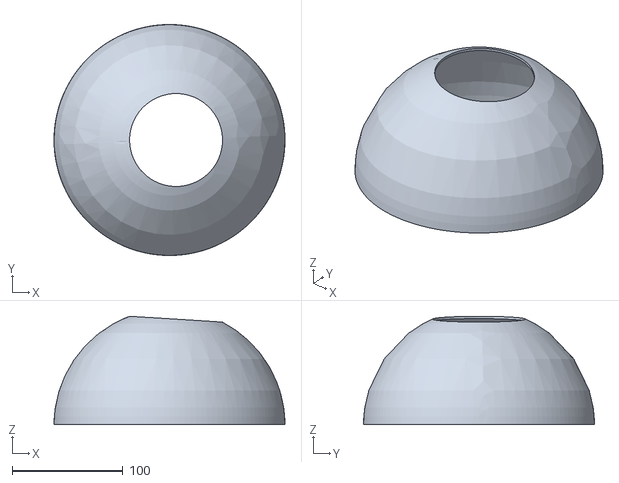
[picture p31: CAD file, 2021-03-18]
_3D Print Files/07-cap.stl
208.2 x 208.2 x 97.7

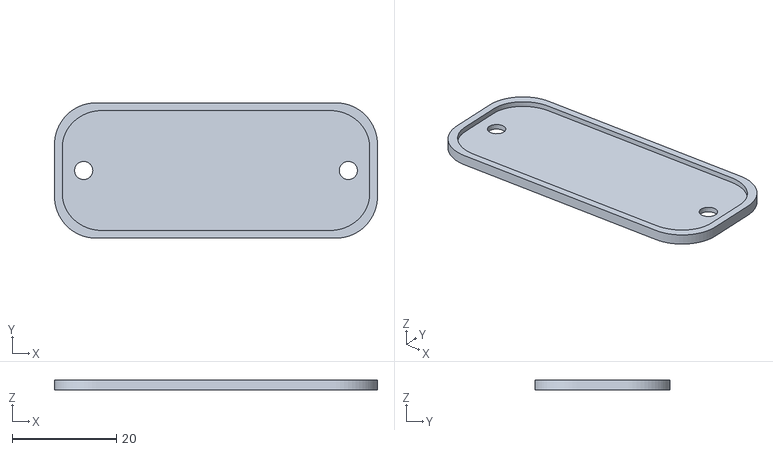
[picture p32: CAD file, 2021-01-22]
__[forked repository OSTR]/V2/docs/Name_Plate.stl
62.0 x 26.0 x 2.00

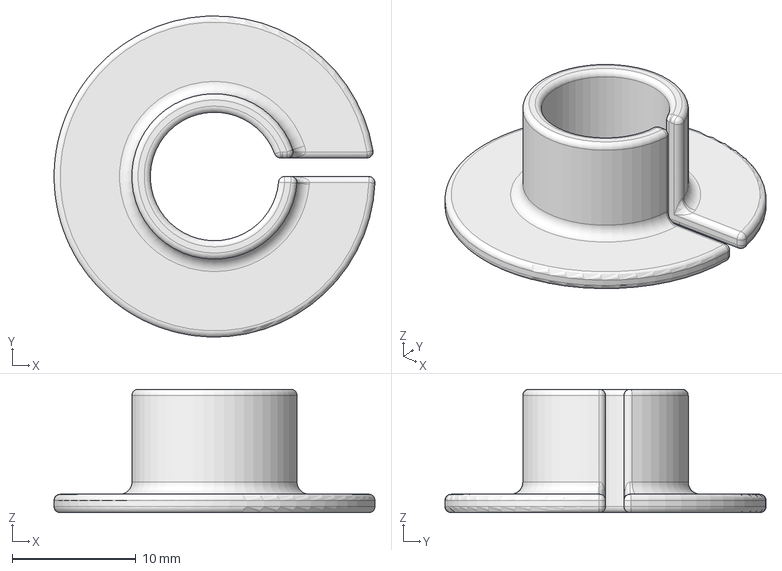
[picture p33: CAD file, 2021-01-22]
__[forked repository OSTR]/V2/mechanical/FreeCad/PenCollar.FCStd
26.0 x 26.0 x 10.0 mm

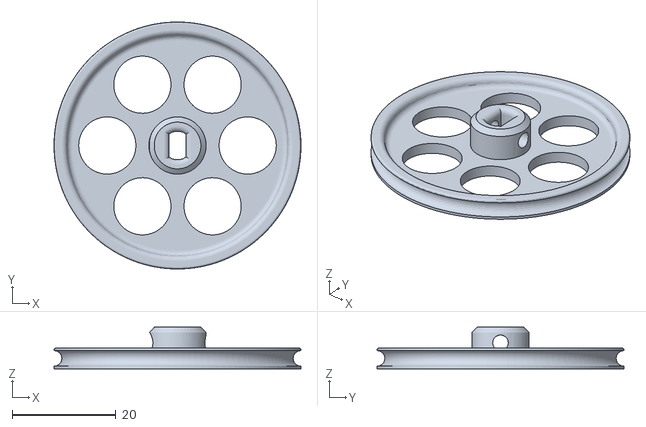
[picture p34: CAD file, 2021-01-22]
__[forked repository OSTR]/V2/mechanical/STL/wheel_47mm_v01.stl
47.5 x 47.5 x 8.00

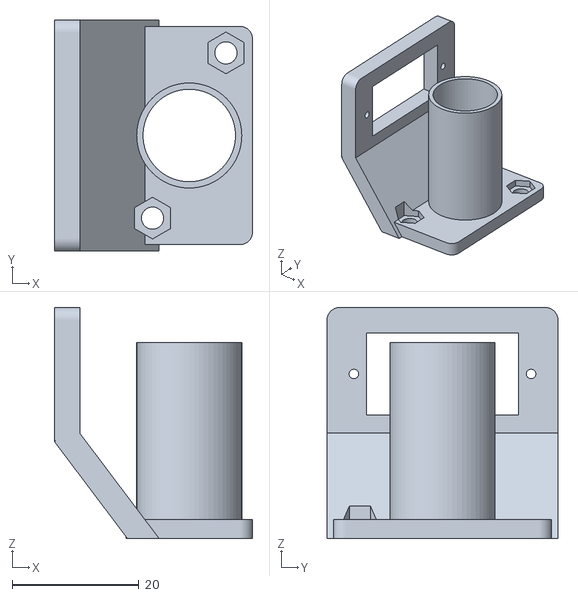
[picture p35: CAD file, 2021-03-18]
_3D Print Files/05-servo-motor-holder.stl
31.3 x 36.5 x 36.5

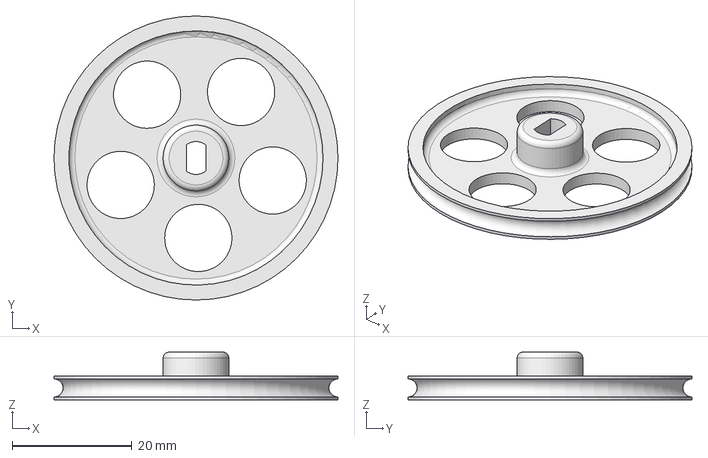
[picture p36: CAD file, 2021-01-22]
__[forked repository OSTR]/V2/mechanical/FreeCad/wheel_v02.FCStd
47.5 x 47.5 x 8.00 mm

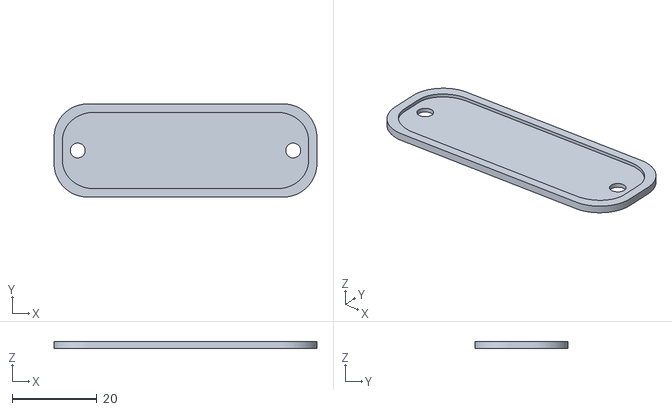
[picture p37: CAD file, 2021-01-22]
__[forked repository OSTR]/V2/mechanical/STL/Nameplate blank.stl
62.0 x 22.0 x 1.60

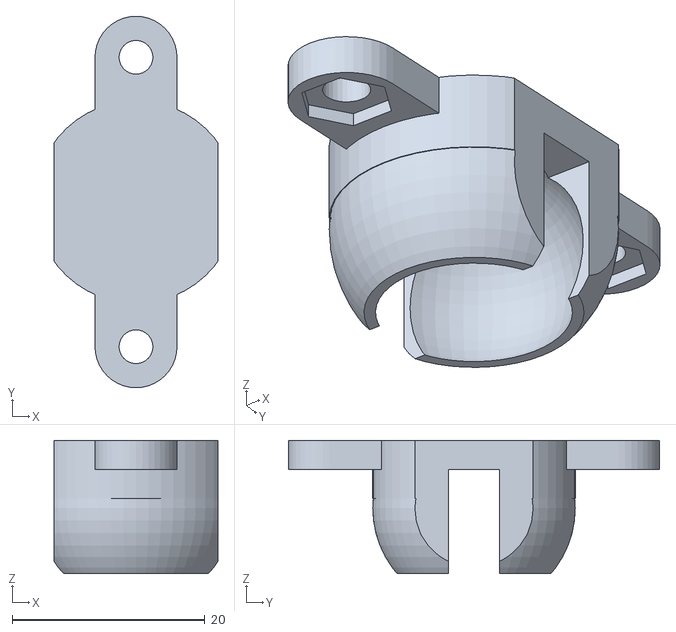
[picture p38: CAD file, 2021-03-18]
_3D Print Files/06-bearing-holder.stl
17.0 x 38.5 x 13.8

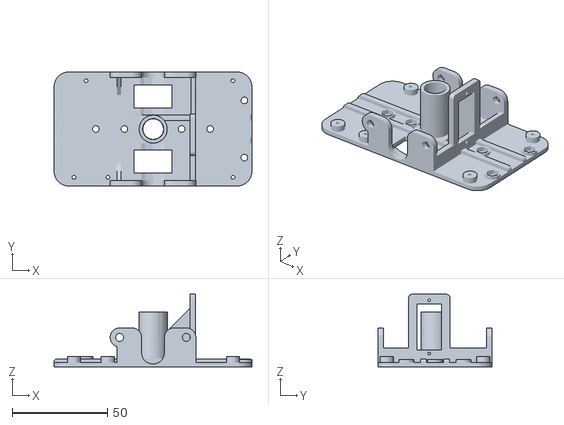
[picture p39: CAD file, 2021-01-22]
__[forked repository OSTR]/V2/mechanical/STL/ItsyBitsy_chassis.stl
104.0 x 60.0 x 38.3

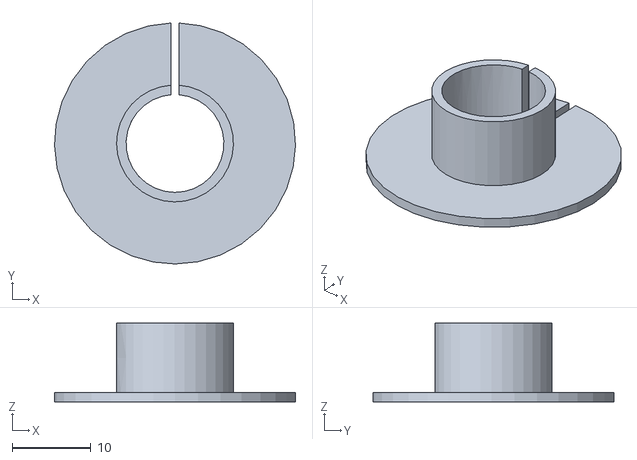
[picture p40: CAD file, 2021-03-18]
_3D Print Files/04-pen-holder.stl
30.5 x 30.5 x 10.0

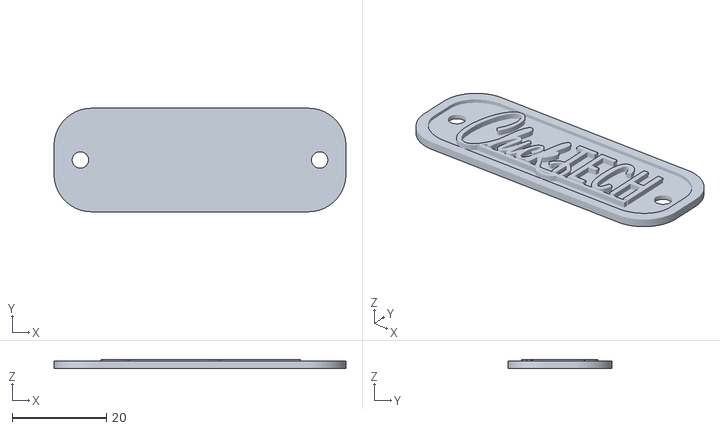
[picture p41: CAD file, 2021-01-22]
__[forked repository OSTR]/V2/mechanical/STL/Nameplate ChickTech.stl
62.0 x 22.0 x 2.00

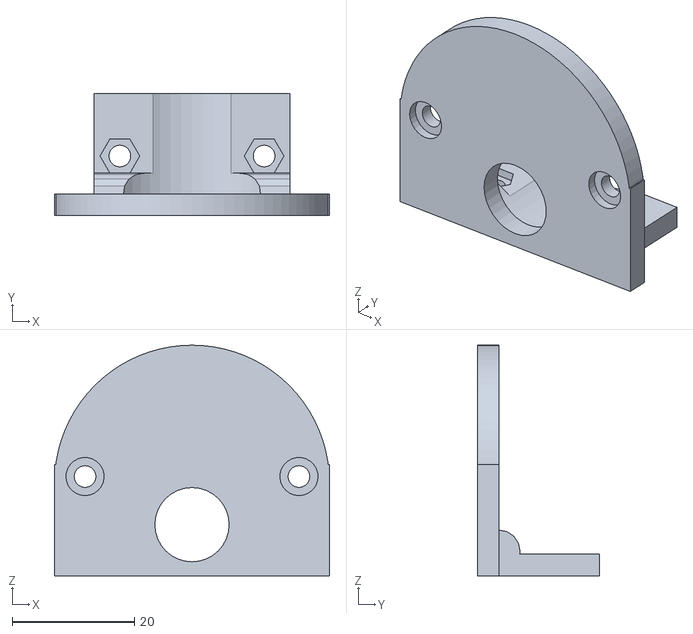
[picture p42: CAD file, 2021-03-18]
_3D Print Files/03-stepper-motor-holder.stl
45.0 x 20.0 x 37.8

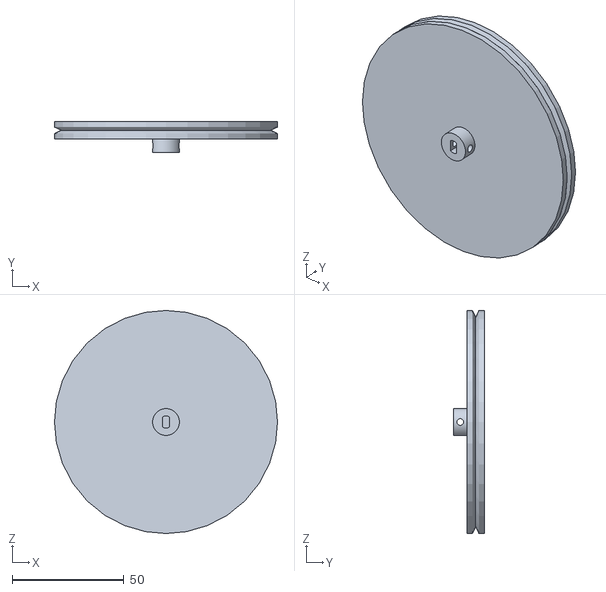
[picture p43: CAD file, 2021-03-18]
_3D Print Files/02-wheel.stl
100.0 x 13.8 x 100.0

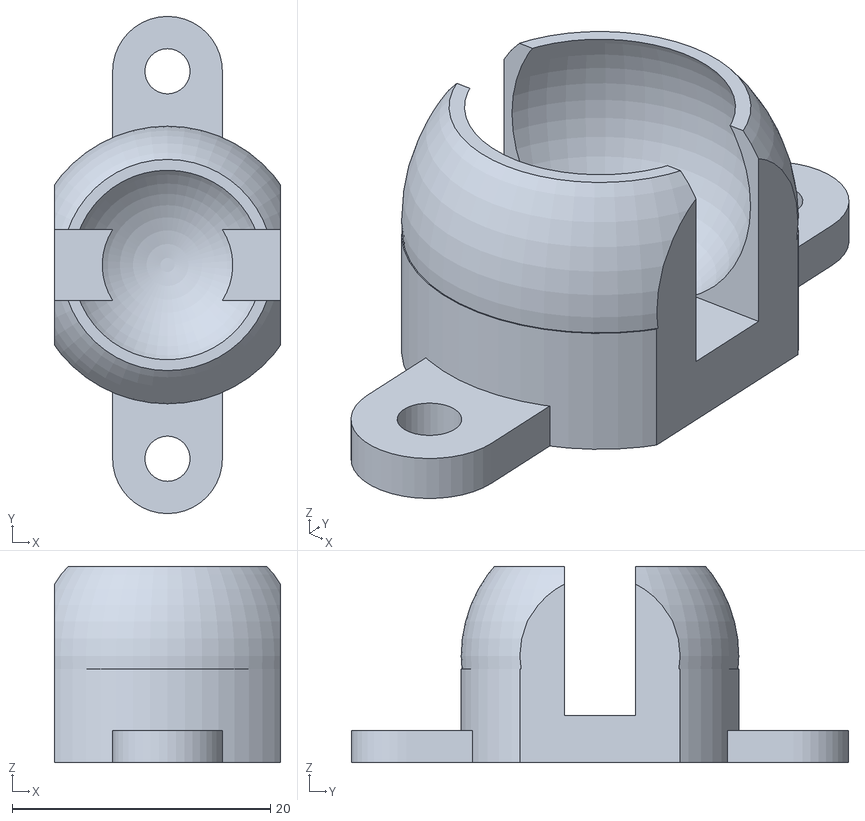
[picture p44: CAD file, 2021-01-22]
__[forked repository OSTR]/V2/mechanical/STL/Caster_18-5.stl
17.5 x 38.5 x 15.2

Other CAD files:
__[forked repository OSTR]/V2/mechanical/STL/PenCollar10-4mm.stl
_3D Print Files/01-base.stl
__[forked repository OSTR]/V2/mechanical/STL/Nameplate Turtle.stl
_3D Print Files/06-bearing-holder-extension.stl
__[forked repository OSTR]/V1/mechanical/OpenSCAD/Caster.scad
__[forked repository OSTR]/V1/mechanical/OpenSCAD/Chassis.scad
__[forked repository OSTR]/V1/mechanical/OpenSCAD/Chassis_MicroBit.scad
__[forked repository OSTR]/V1/mechanical/OpenSCAD/Chassis_Tinsy_V0.scad
_Fabrication Files/CNC/piCamera_CNC_R6.3dm
_Fabrication Files/Lasercut/piCamera_Laser_R6.3dm
_Fabrication Files/Lasercut/piCamera_Laser_R7.3dm
_Hardware/3D Models/3D Model of Drawing Bot_Rhino6.3dm
__[forked repository OSTR]/V1/mechanical/FreeCad/Nameplate.FCStd
__[forked repository OSTR]/V1/mechanical/FreeCad/penCollar.FCStd
__[forked repository OSTR]/V1/mechanical/FreeCad/stepperMount_v01.FCStd
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

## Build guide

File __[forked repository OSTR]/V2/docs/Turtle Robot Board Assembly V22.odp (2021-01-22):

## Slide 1

1. Resistors:

- No polarity
- 330 ohm = orange-orange-brown-gold
- 10K ohm = brown-black-orange-gold

Turtle Robot Board Assembly (V2.2)

Assemble in order indicated.

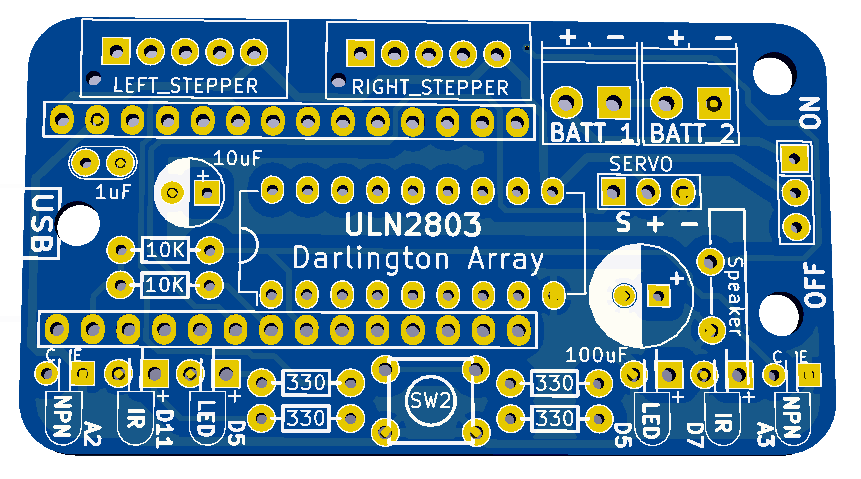
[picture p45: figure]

2. IC socket:

- Match divot on left side.
- Insert chip after Step 8.

3. Button:

- Match legs to holes
- Press to snap in place

4. LEDS / IR / Detector:

- Long leg in square pad.
- Bend leads so they face edge of board.
- Outter: Black IR NPN Detectors(A2, A3)
- Inner: Colored LEDs (D5)
- Middle: Clear IR Emitters (D7, D11)

5. Capacitors:

- 1 uF no polarity “104”
- 10 uF long leg positive, square pad.
- 100 uF long leg positive, square pad.

6.Switch: No polarity

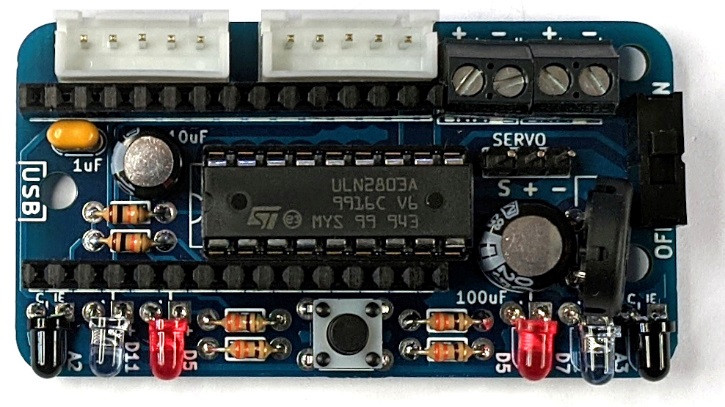
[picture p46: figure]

7. Headers:

- White JST: Slots to edge.
- Black 2-position: Openings to edge.
- Servo 3-position: long legs up

8. Speaker: No polarity.

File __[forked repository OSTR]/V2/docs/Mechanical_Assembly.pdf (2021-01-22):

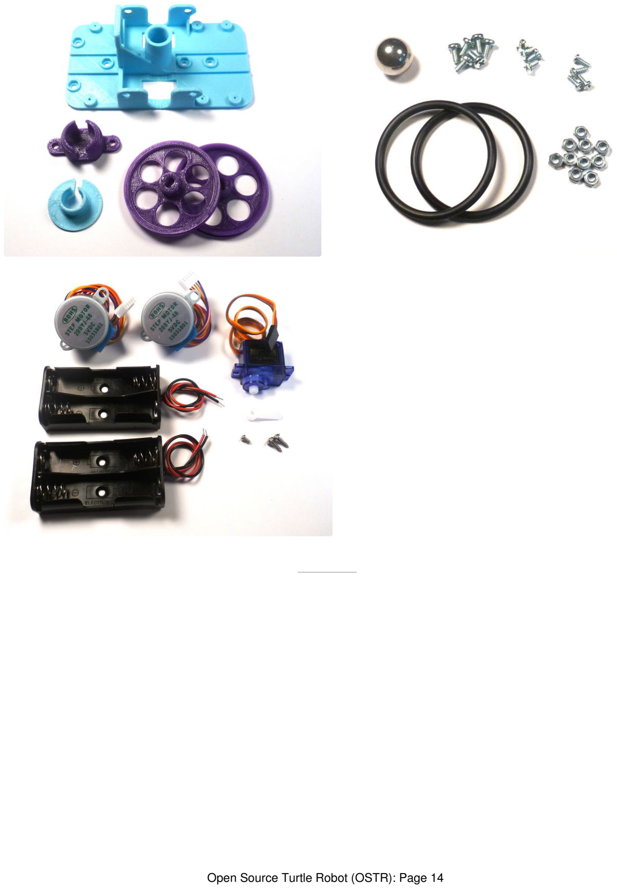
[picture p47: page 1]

Open Source Turtle Robot (OSTR): Page 14

### Step 12: ME: Chassis Prep

A "chassis" is the fame of a motor vehicle or other wheeled conveyance, and in this case the robot's chassis forms the platform for the electronics, motors, and servos.

Time to get familiar with your hardware. We will be using three different types of Phillips screws you will have to be able to identify:

Pan Head Screw (M3 x 6 mm) -> Stepper motors to Chassis Flat Head Screw (M3 x 6 mm) -> Battery Holders to Chassis Round Head Thread-Forming Screw (#2 x 1/4") -> PCB to Chassis

In order to attach parts, we are going to embed M3 nuts into the chassis.

Use an M3 round-head screw and tighten it to pull the nut into the pocket so it is seated flush. Remove the screw.

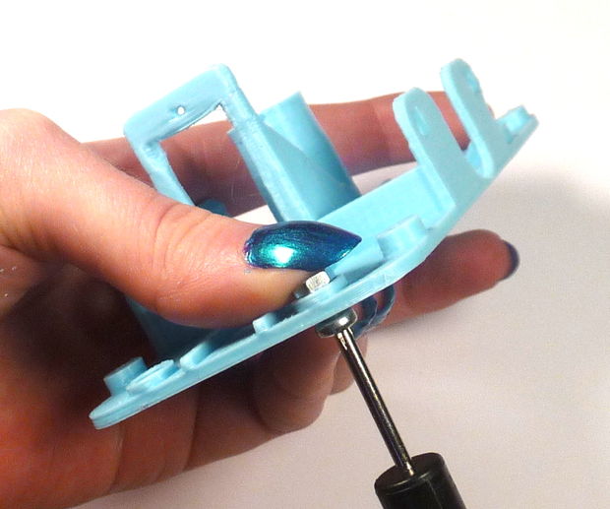
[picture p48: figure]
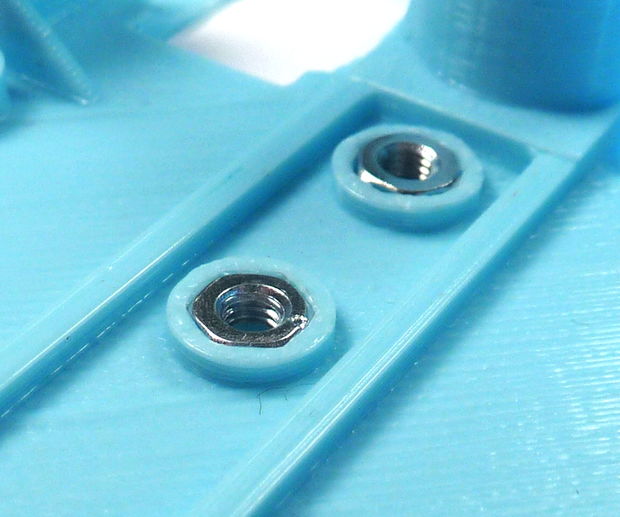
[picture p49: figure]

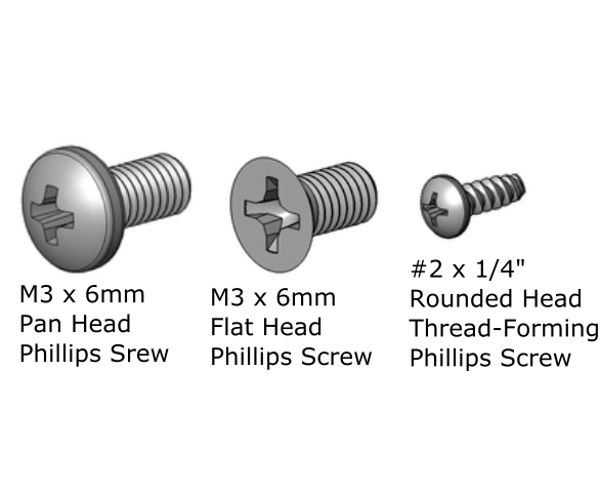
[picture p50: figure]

### Step 13: ME: Batteries

Integrating the electrical components like motors and batteries with the chassis will fall into the ME's domain.

Attach the battery holders using two M3 flat-head screws and thread the wires through the openings under the motor mounts.

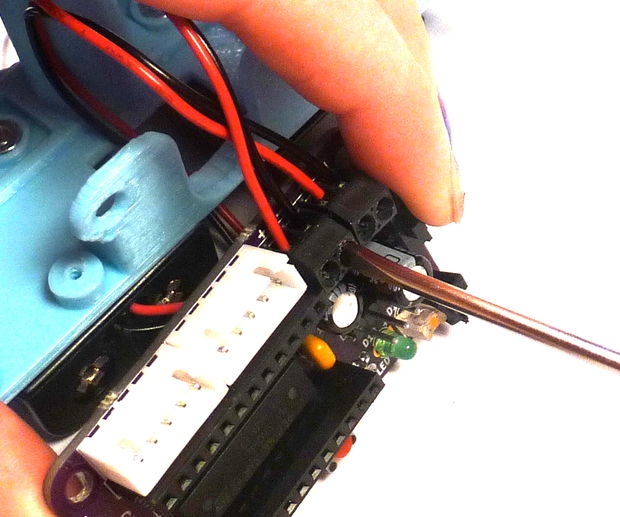
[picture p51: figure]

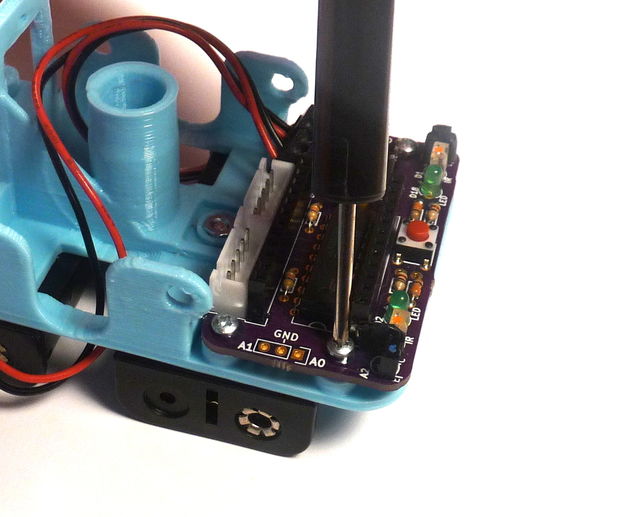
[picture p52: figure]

Put on your "EE" hat and attach the positive and negative wires to the terminals marked "+" and "-", one set of batteries for each terminal.

Attach the circuit board to the chassis using #2x1/4 thread-forming screws.
If the screws wont start, remove the PCB and use the tip of the screw driver to open them up a bit.

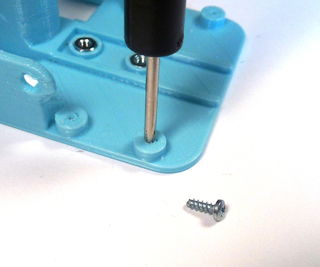
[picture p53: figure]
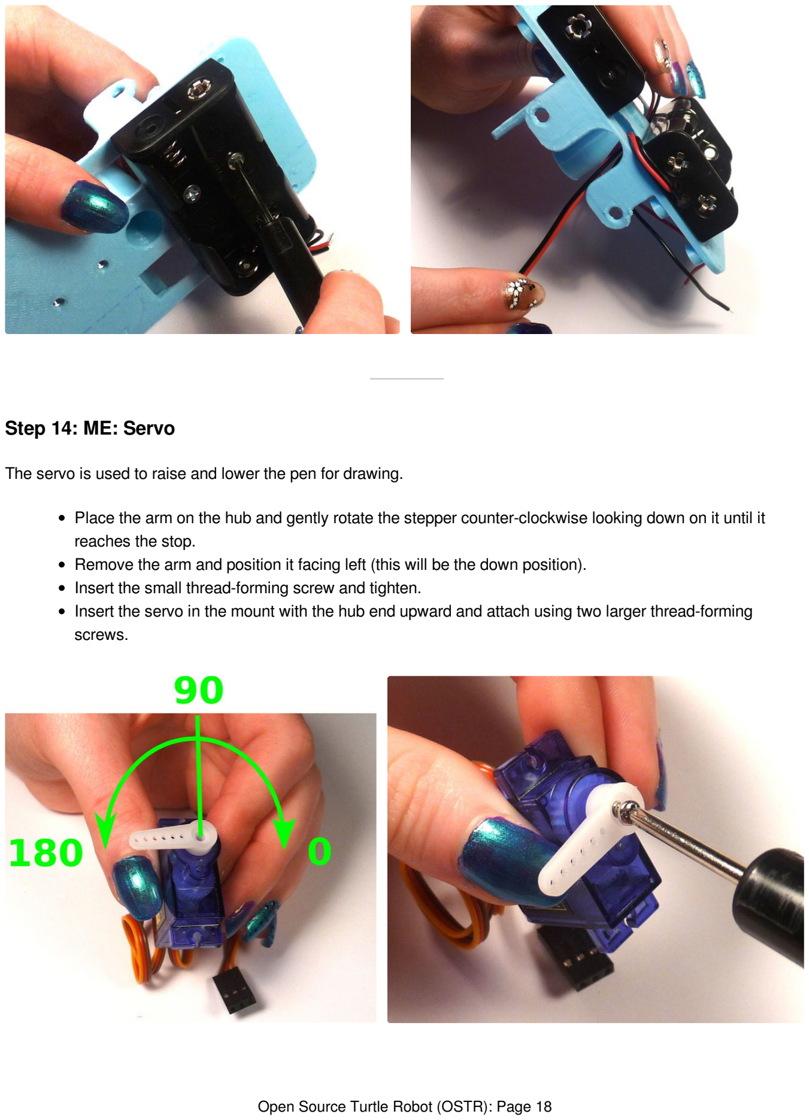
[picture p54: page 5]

### Step 14: ME: Servo

The servo is used to raise and lower the pen for drawing.

Place the arm on the hub and gently rotate the stepper counter-clockwise looking down on it until it reaches the stop.
Remove the arm and position it facing left (this will be the down position).
Insert the small thread-forming screw and tighten.
Insert the servo in the mount with the hub end upward and attach using two larger thread-forming screws.

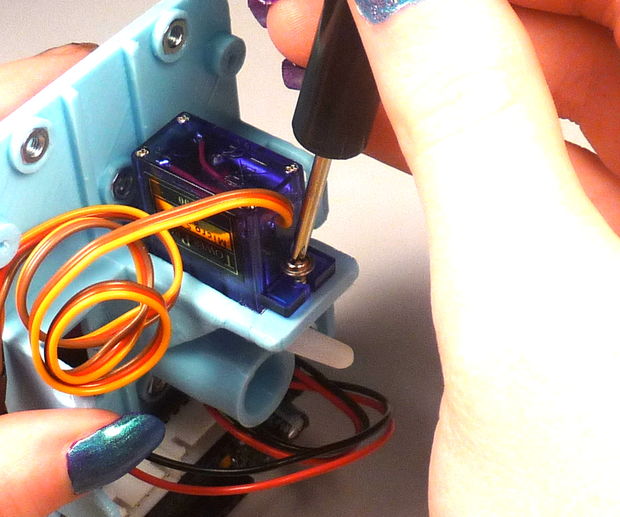
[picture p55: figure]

### Step 15: ME: Stepper Motors

Before we mount the stepper motors, check the fit of the wheels on the shaft. These should slid on fairly tightly if your printer is calibrated correctly.

If they are too tight, use a jewelers file to open up clearance. You can also heat the hub with a hair drier, but do so sparingly to avoid warping the rim.
If they are too loose, you can use an M3 round-head screw to hold the wheel to the shaft (after the motor is mounted).

We are going to pass the wires of the stepper (and servo) under the body to help with wire management.

Start with the left side and thread the wires for the stepper (and servo) through the opening with wires coming from the stepper following down the back side.
Insert the motor into the mount and attach with two M3 round-head screws and nuts.
Gently pull the wires through.

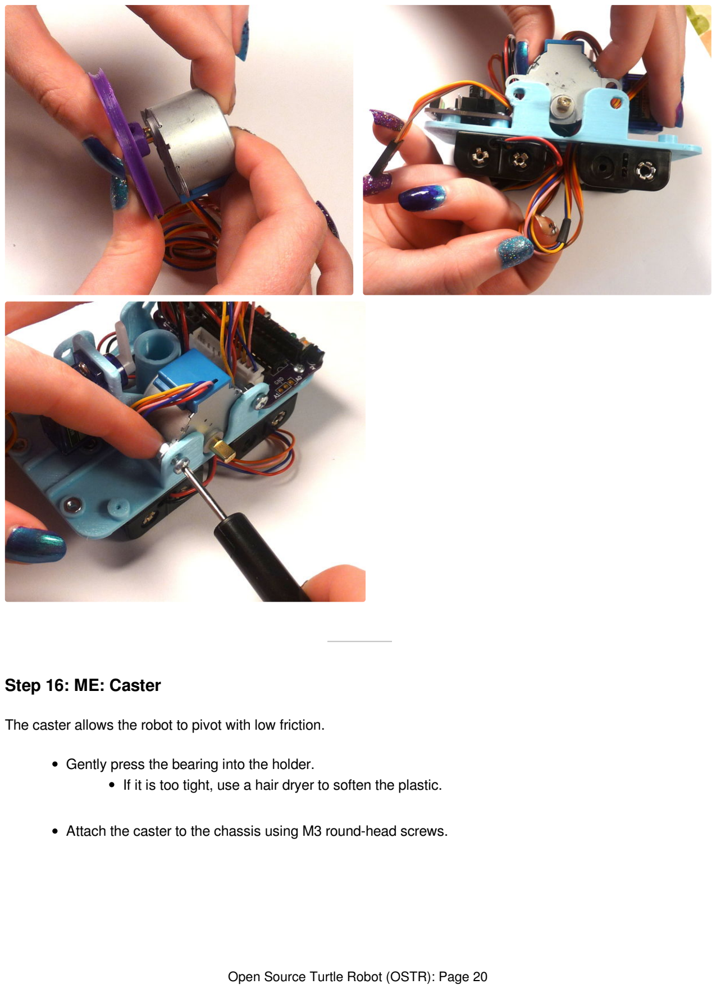
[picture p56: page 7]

### Step 16: ME: Caster

The caster allows the robot to pivot with low friction.

Gently press the bearing into the holder.
If it is too tight, use a hair dryer to soften the plastic.

Attach the caster to the chassis using M3 round-head screws.

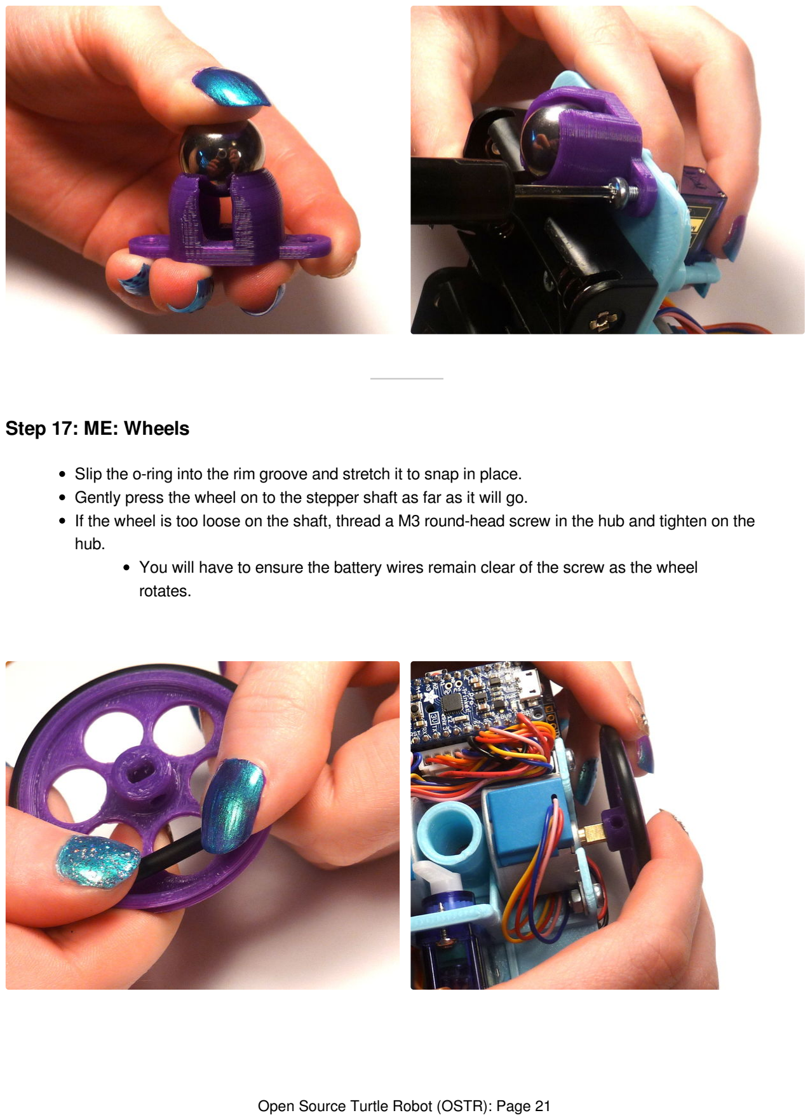
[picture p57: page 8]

### Step 17: ME: Wheels

Slip the o-ring into the rim groove and stretch it to snap in place.
Gently press the wheel on to the stepper shaft as far as it will go.
If the wheel is too loose on the shaft, thread a M3 round-head screw in the hub and tighten on the hub.
You will have to ensure the battery wires remain clear of the screw as the wheel rotates.

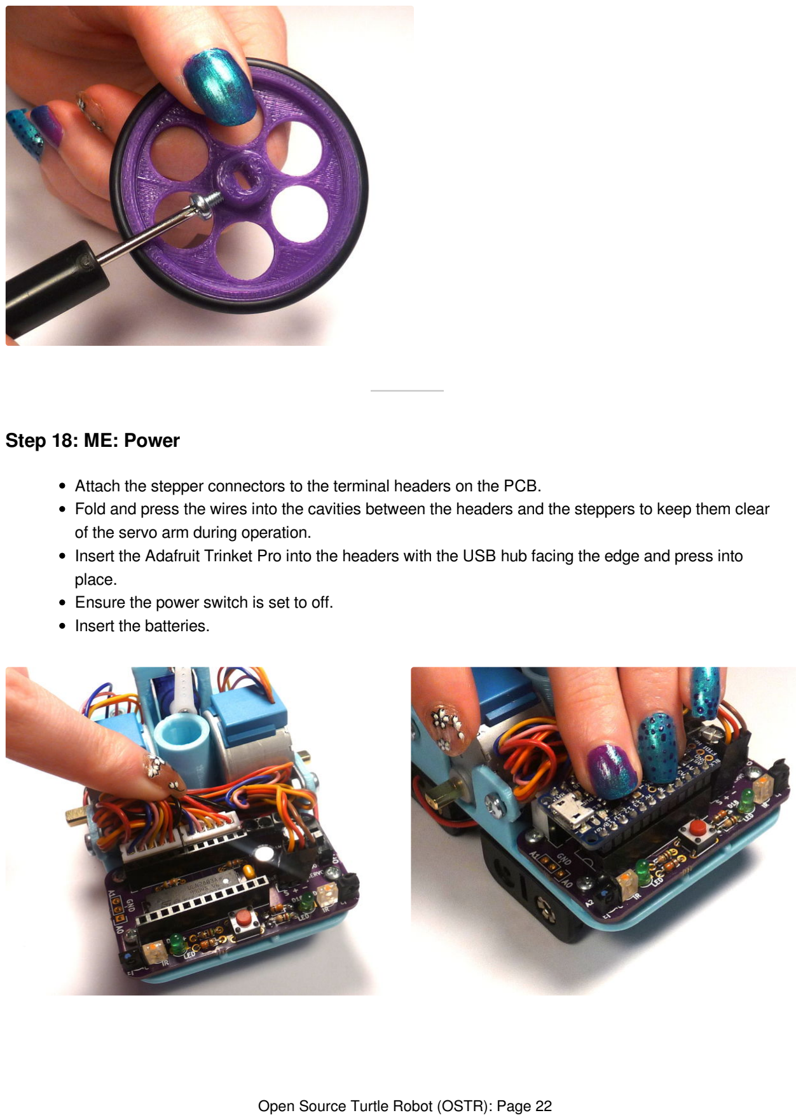
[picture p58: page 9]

### Step 18: ME: Power

Attach the stepper connectors to the terminal headers on the PCB.
Fold and press the wires into the cavities between the headers and the steppers to keep them clear of the servo arm during operation.
Insert the Adafruit Trinket Pro into the headers with the USB hub facing the edge and press into place.
Ensure the power switch is set to off.
Insert the batteries.

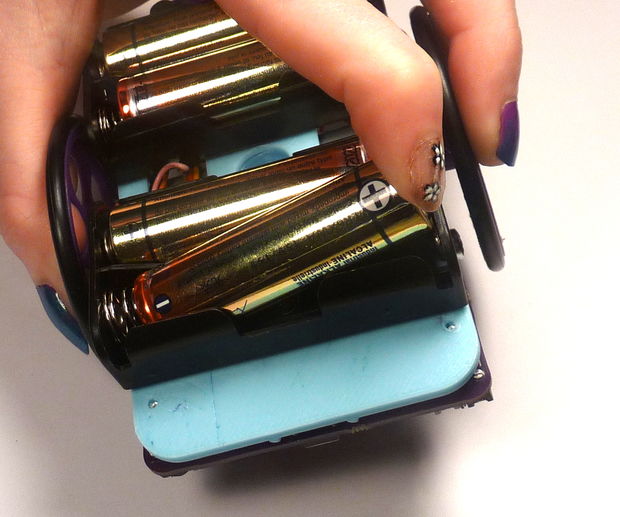
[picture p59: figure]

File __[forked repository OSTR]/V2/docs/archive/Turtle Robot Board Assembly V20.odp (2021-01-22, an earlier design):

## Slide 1

1. Resistors:

- No polarity
- 100 ohm = brown-black-brown-gold
- 330 ohm = orange-orange-brown-gold
- 10K ohm = brown-black-orange-gold

Turtle Robot Board Assembly (V2)

Assemble in order indicated.

7. Headers:

- White JST: Slots outward
- Black 2-position: Openings outward
- Servo 3-position: long legs up

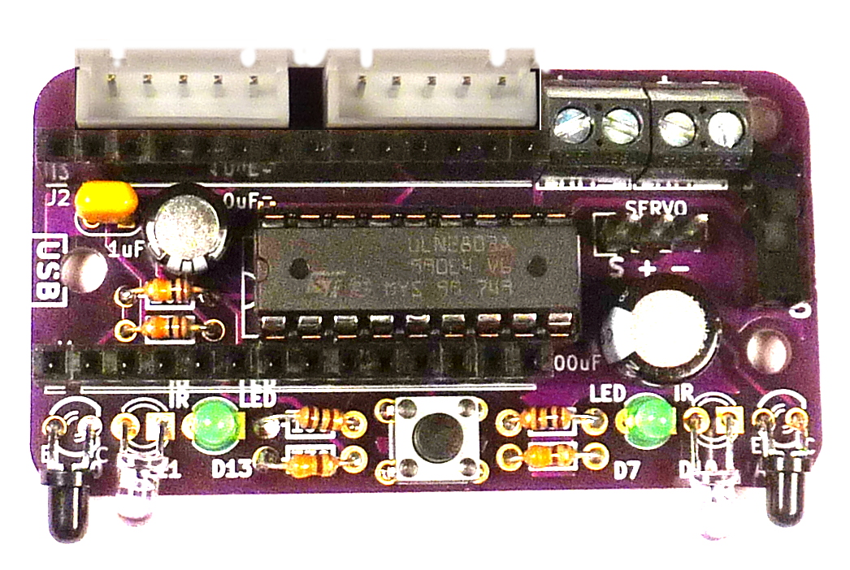
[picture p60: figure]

4. LEDS / IR / Detector:

- LED (D13, D7): long leg is positive. Square Pad
- Bend IR emitter & detector so they face the front:
  - Clear IR Emitter (D11, D10): long leg is positive. Square Pad
  - Black IR Detector (A0, A1): Long leg emmiter (“E”).

2. IC socket:

- Match divot on left side.
- Insert chip after Step 7.

6.Switch:

- No polarity

3. Button:

- Match legs to holes
- Press to snap in place

5. Capacitors:

- 1 uF no polarity “104”
- 10 uF long leg positive
- 100 uF long leg positive

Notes: <number>

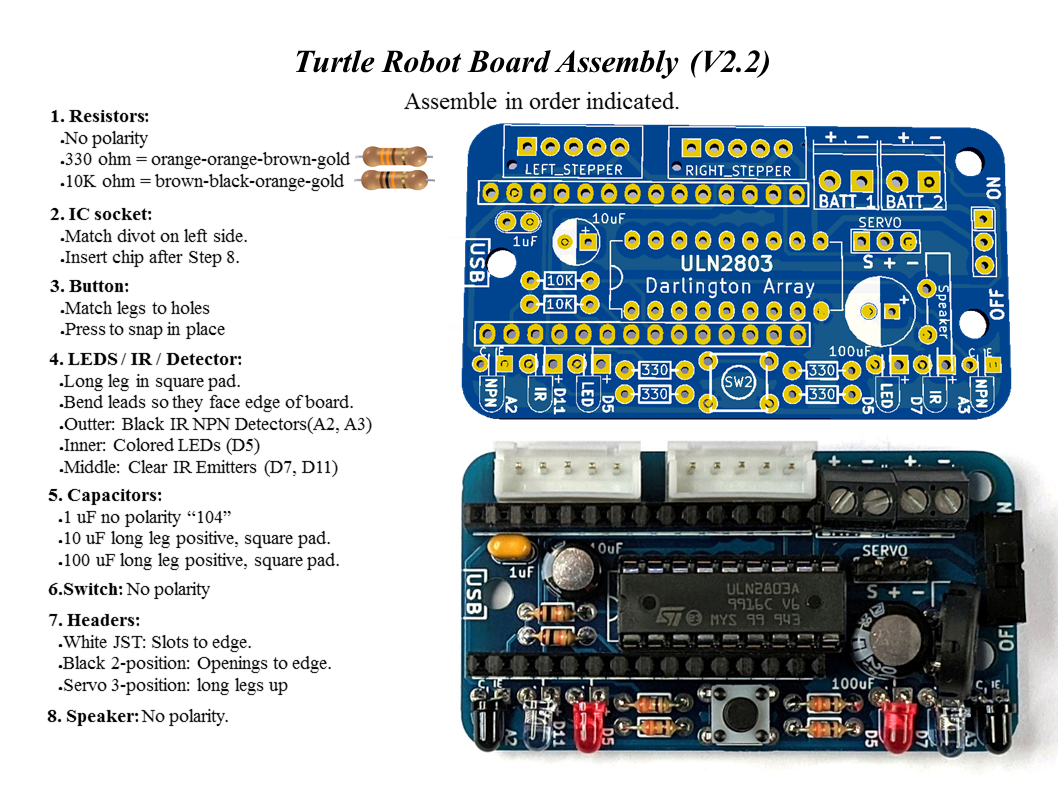
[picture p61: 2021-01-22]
__[forked repository OSTR]/V2/docs/Turtle Robot Board Assembly V22.png

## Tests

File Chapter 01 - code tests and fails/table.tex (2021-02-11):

\documentclass[preview]{standalone}
\begin{document}
\begin{tabular}{|r|r|}
\hline
1 & 2 \\ \hline
3 & 4 \\ \hline
\end{tabular}
\end{document}

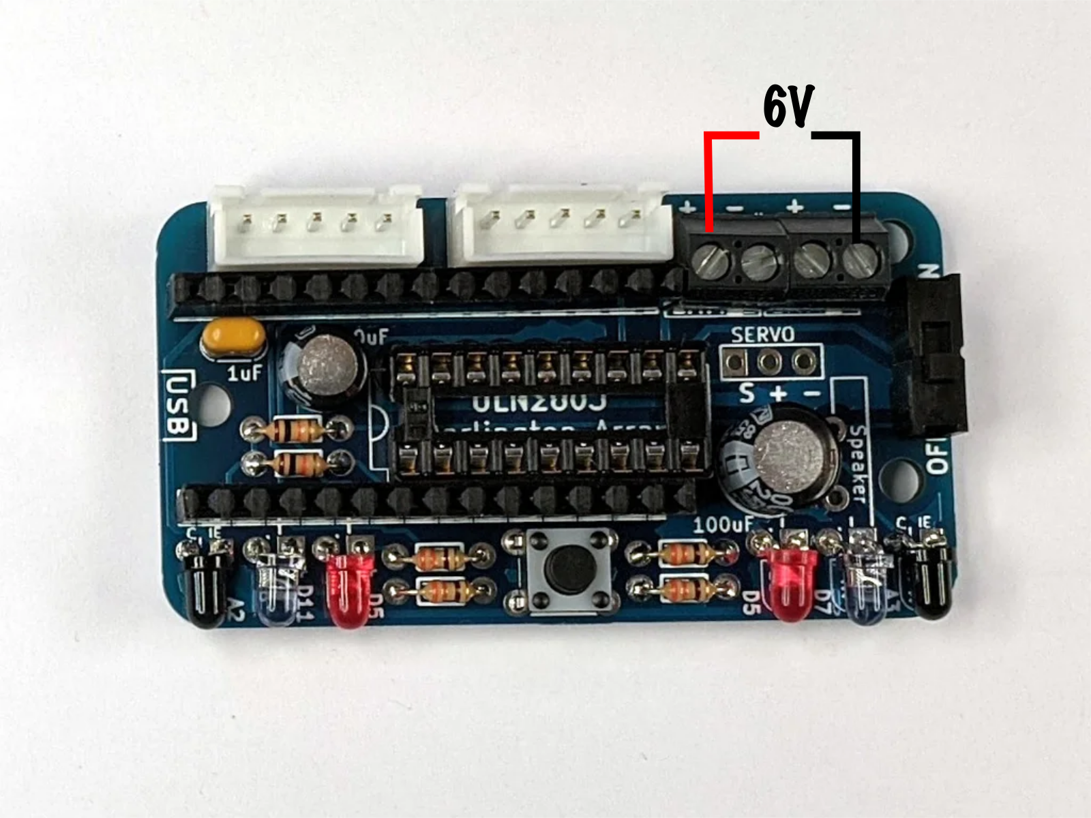
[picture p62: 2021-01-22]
__[forked repository OSTR]/V2/images/battery_test.png

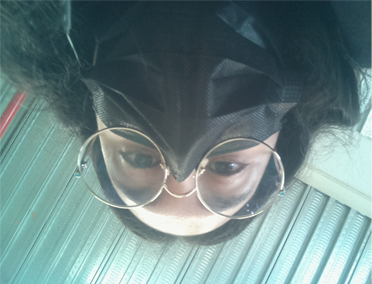
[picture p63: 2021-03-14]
_Scripts/Python_codes/_test_images/image-01-scaled.png

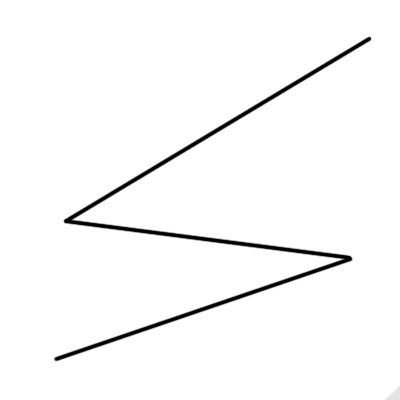
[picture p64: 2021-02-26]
_Scripts/Python_codes/_test_images/sample_tests/400x400pix_test3.png

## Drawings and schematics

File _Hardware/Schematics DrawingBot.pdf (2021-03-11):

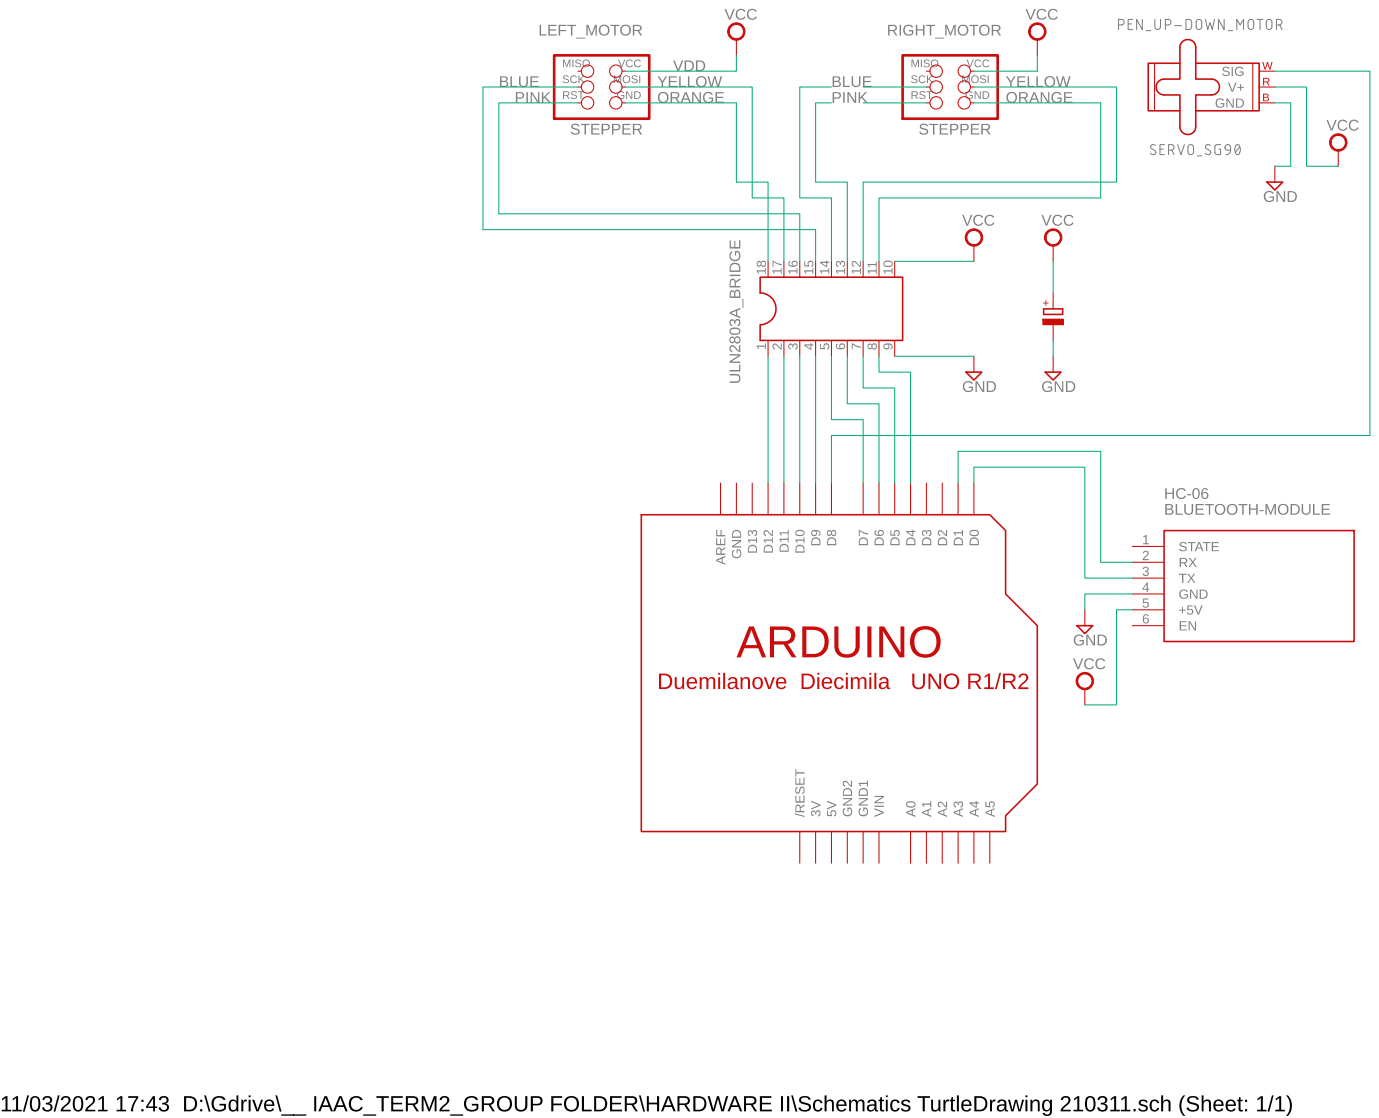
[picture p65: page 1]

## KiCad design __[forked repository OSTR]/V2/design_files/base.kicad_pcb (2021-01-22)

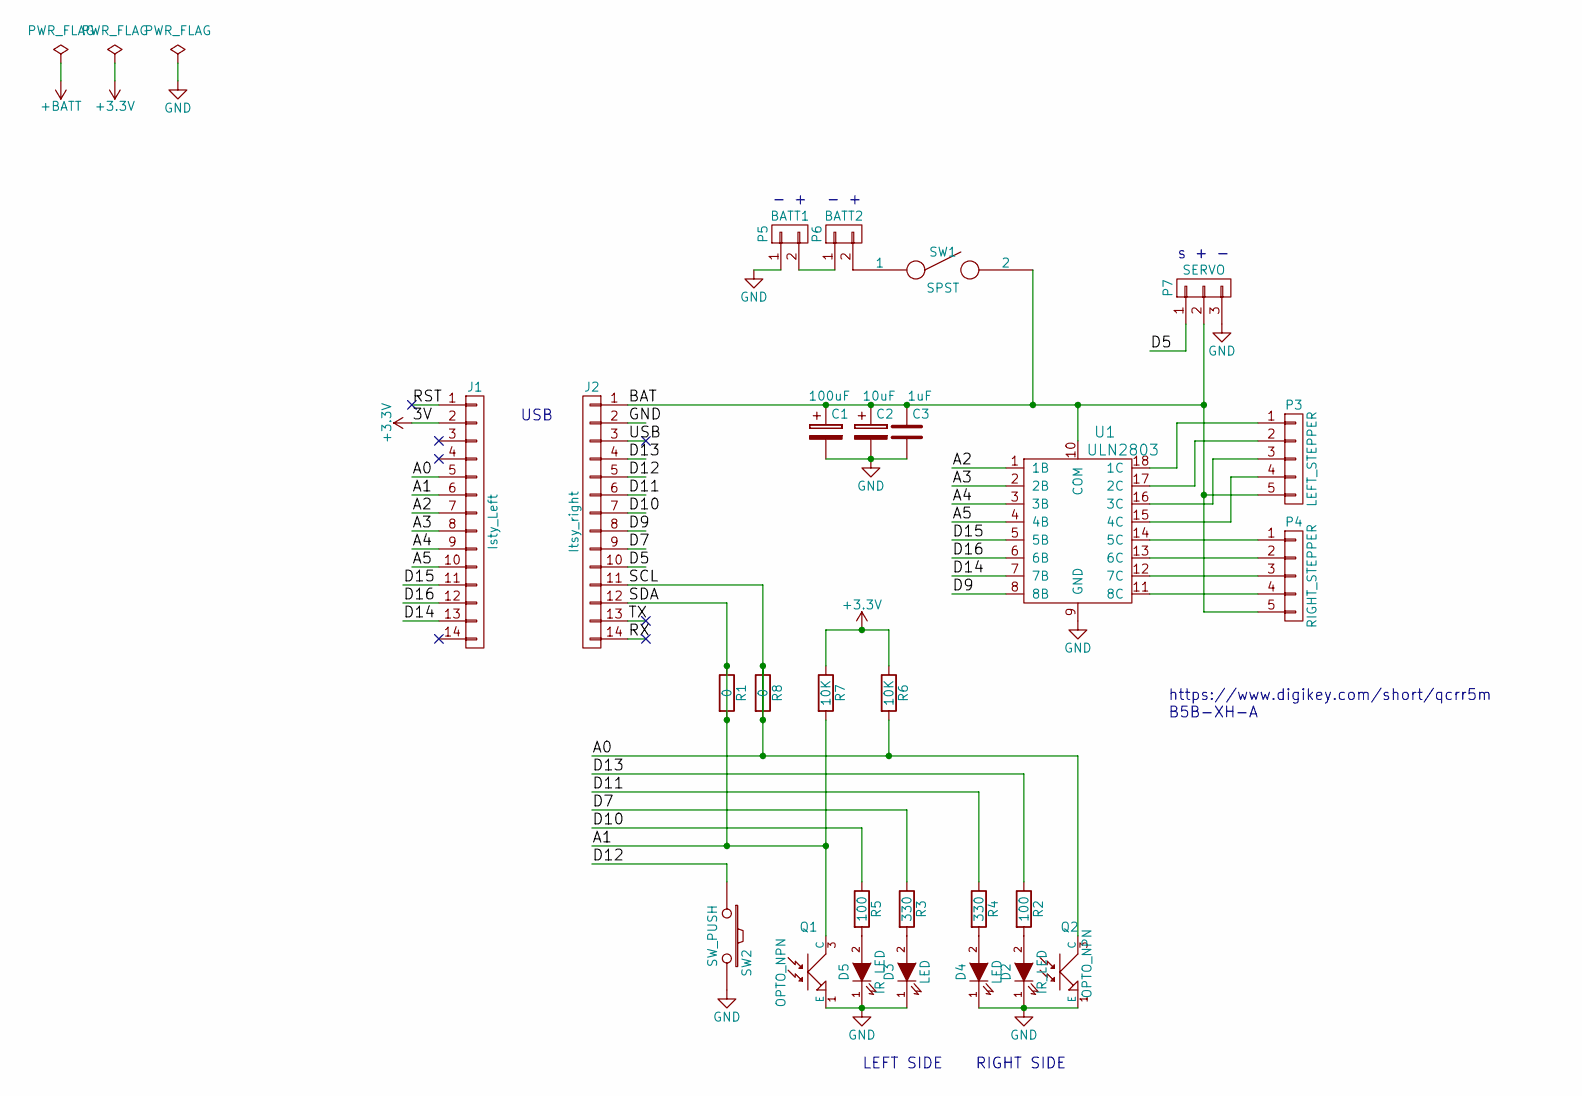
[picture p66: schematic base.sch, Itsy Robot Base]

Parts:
C1: 100uF; C_Radial_D7.5_L11.2_P2.5
C2: 10uF; C_Radial_D5_L11_P2.5
C3: 1uF; C_Disc_D3_P2.5
D2: IR_LED; LED-3MM
D3, D4: LED; LED-3MM
D5: IR LED; LED-3MM
J1: Isty_Left; Pin_Header_Straight_1x14_Pitch2.54mm
J2: Itsy_right; Pin_Header_Straight_1x14_Pitch2.54mm
P3: LEFT_STEPPER; TerminalBlock_Pheonix_MPT-2.54mm_2pol
P4: RIGHT_STEPPER; TerminalBlock_Pheonix_MPT-2.54mm_2pol
P5: BATT1; TerminalBlock_Pheonix_MPT-2.54mm_2pol
P6: BATT2; TerminalBlock_Pheonix_MPT-2.54mm_2pol
P7: SERVO; Pin_Header_Straight_1x03
Q1, Q2: OPTO_NPN; PHOTOTRANS
R1, R8: 0; R_0402
R2, R5: 100; Resistor_Horz
R3, R4: 330; Resistor_Horz
R6, R7: 10K; Resistor_Horz
SW1: SPST; SW_Micro_SPST
SW2: SW_PUSH; SW_PUSH_SMALL
U1: ULN2803; DIP-18_W7.62mm

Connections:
+3V3: J1.2, R6.1, R7.1
/A0: J1.5, J2.11, Q2.3 (C), R6.2, R8.1, R8.2
/A1: J1.6, J2.12, Q1.3 (C), R1.1, R1.2, R7.2
/A2: J1.7, U1.1 (1B)
/A3: J1.8, U1.2 (2B)
/A4: J1.9, U1.3 (3B)
/A5: J1.10, U1.4 (4B)
/BAT: C1.1, C2.1, C3.1, J2.1, P3.5, P4.5, P7.2, SW1.2, U1.10 (COM)
/D5: J2.10, P7.1
/D7: J2.9, R3.1
/D9: J2.8, U1.8 (8B)
/D10: J2.7, R5.1
/D11: J2.6, R4.1
/D12: J2.5, SW2.1
/D13: J2.4, R2.1
/D14: J1.13, U1.7 (7B)
/D15: J1.11, U1.5 (5B)
/D16: J1.12, U1.6 (6B)
/RST: J1.1
/RX: J2.14
/TX: J2.13
/USB: J2.3
GND: C1.2, C2.2, C3.2, D2.1 (K), D3.1 (K), D4.1 (K), D5.1 (K), J2.2, P5.1, P7.3, Q1.1 (E), Q2.1 (E), SW2.2, U1.9 (GND)
unnamed: D2.2 (A), R2.2
unnamed: D3.2 (A), R3.2
unnamed: D4.2 (A), R4.2
unnamed: D5.2 (A), R5.2
unnamed: P3.1, U1.18 (1C)
unnamed: P3.2, U1.17 (2C)
unnamed: P3.3, U1.16 (3C)
unnamed: P3.4, U1.15 (4C)
unnamed: P4.1, U1.14 (5C)
unnamed: P4.2, U1.13 (6C)
unnamed: P4.3, U1.12 (7C)
unnamed: P4.4, U1.11 (8C)
unnamed: P5.2, P6.1
unnamed: P6.2, SW1.1

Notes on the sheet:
https://www.digikey.com/short/qcrr5m B5B-XH-A
USB
- +
s + -
LEFT SIDE RIGHT SIDE

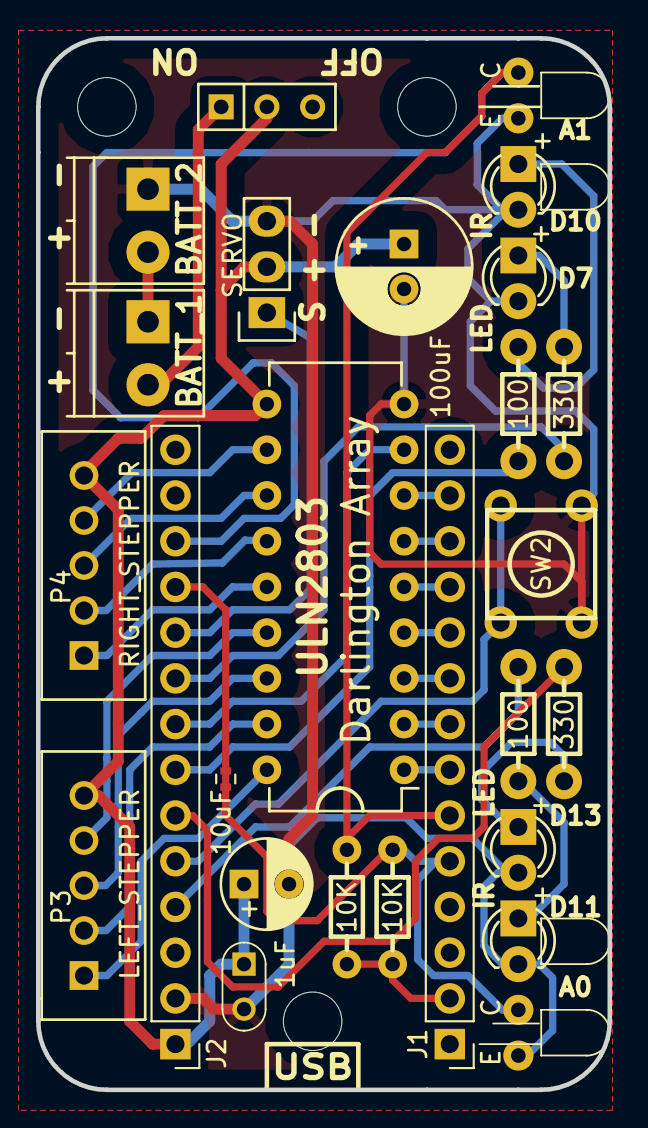
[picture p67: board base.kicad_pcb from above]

Board: 2 copper layers, 31.8 x 58.4 mm, 32 parts (1 on the bottom side), 33 nets.

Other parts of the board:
P9, P9#2, P9#3: CONN_01X01; Lego_Pad
VAL: MadeInOregonRev25
VAL#2: MB225rev

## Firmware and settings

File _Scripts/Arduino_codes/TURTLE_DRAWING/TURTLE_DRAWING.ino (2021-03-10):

// This code is based on the code from https://github.com/aspro648/OSTR
// The modification that was made has the objective of controlling the TurtleBot through the Serial Monitor
// The code to read the Serial Monitor it is based in the code from https://www.automatizacionparatodos.com/puerto-serie-arduino/
// instead of writing all the instructions for the turtle in this sketch
// The instructions that can be sent through the Serial Monitor can be:
// 'U' for penup
// 'D' for pendown
// 'F100' for move forward 100 mm or any number
// 'B100' for move backward 100 mm or any number 
// 'R45' to rotate right 45 degrees or any number
// 'L45' to rotate right 45 degrees or any number
// only capitals letters


#include <Servo.h>

// - - - - - - - - - - - - - - - - - - - - - - - - - - - - - - - - - - - -
// STRING DESCRIPTION
String entradaSerial = "";     // String for the instruction
bool entradaCompleta = false;  // 
// - - - - - - - - - - - - - - - - - - - - - - - - - - - - - - - - - - - -


// - - - - - - - - - - - - - - - - - - - - - - - - - - - - - - - - - - - -
// SETUP SERVO
int servoPin = 8;
int PEN_DOWN = 80; // angle of servo when pen is down
int PEN_UP = 20;   // angle of servo when pen is up
Servo penServo;
// - - - - - - - - - - - - - - - - - - - - - - - - - - - - - - - - - - - -

// - - - - - - - - - - - - - - - - - - - - - - - - - - - - - - - - - - - -
// CALIBRATION OF WHEELS
float wheel_dia = 62; //    # mm (increase = spiral out)
float wheel_base = 115; //    # mm (increase = spiral in, ccw)
int steps_rev = 512; //        # 512 for 64x gearbox, 128 for 16x gearbox
int delay_time = 6; //         # time between steps in ms
// - - - - - - - - - - - - - - - - - - - - - - - - - - - - - - - - - - - -

// - - - - - - - - - - - - - - - - - - - - - - - - - - - - - - - - - - - -
// STEPPER SEQUENCE org->pink->blue->yel
int L_stepper_pins[] = {12, 10, 9, 11};
int R_stepper_pins[] = {4, 6, 7, 5};
int fwd_mask[][4] =  {{1, 0, 1, 0},
  {0, 1, 1, 0},
  {0, 1, 0, 1},
  {1, 0, 0, 1}
};
int rev_mask[][4] =  {{1, 0, 0, 1},
  {0, 1, 0, 1},
  {0, 1, 1, 0},
  {1, 0, 1, 0}
};
// - - - - - - - - - - - - - - - - - - - - - - - - - - - - - - - - - - - -


void setup() {
  
  randomSeed(analogRead(1));
  Serial.begin(9600);
  for (int pin = 0; pin < 4; pin++) {
    pinMode(L_stepper_pins[pin], OUTPUT);
    digitalWrite(L_stepper_pins[pin], LOW);
    pinMode(R_stepper_pins[pin], OUTPUT);
    digitalWrite(R_stepper_pins[pin], LOW);
  }
  penServo.attach(servoPin);
  Serial.println("setup ready... waiting for instructions");
  Serial.println(entradaSerial);
  penup();
  delay(1000);
}

void loop()
{

   String a = entradaSerial;
   int searchF = a.indexOf('F');
   int d = a.charAt(0);
   int b = a.toInt();
   String w = "waiting for instruction like F100; R20; L45; B200..."; 
 
   if (entradaCompleta) {
    if (entradaSerial == "\n") {
      Serial.print("write instruction. No data received after return\n");
      penup();
      Serial.flush();
    } 
      else if (a.charAt(0) == 'F') {
      a.remove(0, 1);
      int f = a.toInt(); 
      Serial.println("ACK");
      forward(f);
      Serial.flush();
      Serial.println("DONE");
      Serial.flush();
    } 
      else if (a.charAt(0) == 'B') {
      a.remove(0, 1);
      int b = a.toInt();
      Serial.println("ACK");
      backward(b);
      Serial.flush();
      Serial.println("DONE");
      Serial.flush();
    }
      else if (a.charAt(0) == 'R') {
      a.remove(0, 1);
      int r = a.toInt();
      Serial.println("ACK");
      right(r);
      Serial.flush();
      Serial.println("DONE");
      Serial.flush();
    }     
      else if (a.charAt(0) == 'L') {
      a.remove(0, 1);
      int l = a.toInt();
      Serial.println("ACK");
      left(l);
      Serial.flush();
      Serial.println("DONE");
      Serial.flush();
    } 
      else if (a.charAt(0) == 'U') {
      a.remove(0, 1);
      int u = a.toInt();
      Serial.println("ACK");
      penup();
      Serial.flush();
      Serial.println("DONE");
      Serial.flush();
    }
      else if (a.charAt(0) == 'D') {
      a.remove(0, 1);
      int u = a.toInt();
      Serial.println("ACK");
      pendown();
      Serial.flush();
      Serial.println("DONE");
      Serial.flush();
    }             
      else {
      Serial.println(w); 
    }
      entradaCompleta = false;
      entradaSerial = "";
}
}

// - - - - - - - - - - - - - - - - - - - - - - - - - - - - - - - - - - - -
// - - - - - - - - - - - - - - - - - - - - - - - - - - - - - - - - - - - -
// HELPER FUNCTIONS
// - - - - - - - - - - - - - - - - - - - - - - - - - - - - - - - - - - - -
int step(float distance) {
  int steps = distance * steps_rev / (wheel_dia * 3.1412); //24.61
  /*
    Serial.print(distance);
    Serial.print(" ");
    Serial.print(steps_rev);
    Serial.print(" ");
    Serial.print(wheel_dia);
    Serial.print(" ");
    Serial.println(steps);
    delay(1000);*/
  return steps;
}
// - - - - - - - - - - - - - - - - - - - - - - - - - - - - - - - - - - - -
// HELPER FUNCTIONS - TURTLE INSTRUCTIONS
// - - - - - - - - - - - - - - - - - - - - - - - - - - - - - - - - - - - -
// - - - - - - - - - - - - - - - - - - - - - - - - - - - - - - - - - - - -

void forward(float distance) {
  int steps = step(distance);
  //Serial.println(steps);
  for (int step = 0; step < steps; step++) {
    for (int mask = 0; mask < 4; mask++) {
      for (int pin = 0; pin < 4; pin++) {
        digitalWrite(L_stepper_pins[pin], rev_mask[mask][pin]);
        digitalWrite(R_stepper_pins[pin], fwd_mask[mask][pin]);
      }
      delay(delay_time);
    }
  }
}


void backward(float distance) {
  int steps = step(distance);
  for (int step = 0; step < steps; step++) {
    for (int mask = 0; mask < 4; mask++) {
      for (int pin = 0; pin < 4; pin++) {
        digitalWrite(L_stepper_pins[pin], fwd_mask[mask][pin]);
        digitalWrite(R_stepper_pins[pin], rev_mask[mask][pin]);
      }
      delay(delay_time);
    }
  }
}


void right(float degrees) {
  float rotation = degrees / 360.0;
  float distance = wheel_base * 3.1412 * rotation;
  int steps = step(distance);
  for (int step = 0; step < steps; step++) {
    for (int mask = 0; mask < 4; mask++) {
      for (int pin = 0; pin < 4; pin++) {
        digitalWrite(R_stepper_pins[pin], rev_mask[mask][pin]);
        digitalWrite(L_stepper_pins[pin], rev_mask[mask][pin]);
      }
      delay(delay_time);
    }
  }
}


void left(float degrees) {
  float rotation = degrees / 360.0;
  float distance = wheel_base * 3.1412 * rotation;
  int steps = step(distance);
  for (int step = 0; step < steps; step++) {
    for (int mask = 0; mask < 4; mask++) {
      for (int pin = 0; pin < 4; pin++) {
        digitalWrite(R_stepper_pins[pin], fwd_mask[mask][pin]);
        digitalWrite(L_stepper_pins[pin], fwd_mask[mask][pin]);
      }
      delay(delay_time);
    }
  }
}


void done() { // unlock stepper to save battery
  for (int mask = 0; mask < 4; mask++) {
    for (int pin = 0; pin < 4; pin++) {
      digitalWrite(R_stepper_pins[pin], LOW);
      digitalWrite(L_stepper_pins[pin], LOW);
    }
    delay(delay_time);
  }
}


void penup() {
  delay(250);
  penServo.write(PEN_UP);
  delay(250);
}


void pendown() {
  delay(250);
  penServo.write(PEN_DOWN);
  delay(250);
}


void serialEvent() {
  while (Serial.available()) {
    // Obtener bytes de entrada:
    char inChar = (char)Serial.read();
    // Agregar al String de entrada:
    entradaSerial += inChar;
    // Para saber si el string está completo, se detendrá al recibir
    // el caracter de retorno de línea ENTER \n
    if (inChar == '\n') {
      entradaCompleta = true;
    }
  }
}

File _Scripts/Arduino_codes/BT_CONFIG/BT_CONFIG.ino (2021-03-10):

// This code was written by TechKrowd and you can find it at https://github.com/TechKrowd/ArduinoBluetooth
// The tutorial video to set up the HC-06 Bluetooth module is also available at https://www.youtube.com/watch?v=M7DTEcdzDTI
// To set up the HC-06 Bluetooth module you first need to plug the VCC into the digital pin 12 from the Arduino
// You need to do this only the first time to set up the module. Then you can connect it at the 5 volts pin
// The TX from the module goes into RX of the Arduino
// The RX from the module goes into the TX of the Arduino
// After load this sketch into the module you can load any skecth into the Arduino
// Just unplug the RX and TX pins to make it possible to connect with the usb to the computer

const int LED = 13;
const int BTPWR = 12; //after load this skecth you need to plug the pin into the VCC pin

char nombreBT[10] = "turtleBT"; //the name of the bluetooth
char velocidad = '4'; //9600
char pin [5]= "0000"; //pasword to acces the bluetooth module


void setup() {
  pinMode(LED, OUTPUT);
  pinMode(BTPWR, OUTPUT);

  digitalWrite(LED, LOW);
  digitalWrite(BTPWR, HIGH);

  Serial.begin(9600); 

  Serial.print("AT");
  delay(1000);

  Serial.print("AT+NAME");
  Serial.print(nombreBT);
  delay(1000);

  Serial.print("AT+BAUD");
  Serial.print(velocidad);
  delay(1000);

  Serial.print("AT+PIN");
  Serial.print(pin);
  delay(1000);

  digitalWrite(LED, HIGH);
}

void loop() {

}

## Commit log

2021-01-22 new folder
    [Caster.scad, Caster_18-5.stl, Chassis.scad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]
2021-01-22 file name change
    [Caster.scad, Caster_18-5.stl, Chassis.scad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]
2021-02-11 Latest files
    [ArrayShape.csv, ArrayShape1.csv]
2021-02-12 update csv woohoo
    [ArrayShape1.csv]
2021-02-17 latest updates+new files
    [ArrayShape1.csv, CntArrayShape1.csv]
2021-02-23 second folder + latest code
    [ArrayShape.csv, ArrayShape1.csv, CntArrayShape1.csv]
2021-03-10 arduino codes uploaded
2021-03-11 hardware schematics and data sheet
2021-03-11 clean repository and latest files
    [ArrayShape.csv, ArrayShape1.csv, Caster.scad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]
2021-03-11 drawing bot model added
    [3D Model of Drawing Bot_Rhino6.3dm]
2021-03-11 piCamera 3D file up
    [piCamera_CNC_R6.3dm]
2021-03-12 python scripts for arduino communication
2021-03-14 latest changes
    [piCamera_CNC_R6.3dm]
2021-03-18 latest changes to repo
    [ArrayShape.csv, ArrayShape1.csv, Caster.scad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]
2021-03-18 updated repo and md file
    [01-base.stl, 02-wheel.stl, 03-stepper-motor-holder.stl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]
2021-03-18 fabrication update
    [piCamera_CNC_R6.3dm]
2021-03-18 fabrication update laser file
    [piCamera_Laser_R6.3dm, piCamera_Laser_R7.3dm]
2021-03-19 raspberry pi info added
